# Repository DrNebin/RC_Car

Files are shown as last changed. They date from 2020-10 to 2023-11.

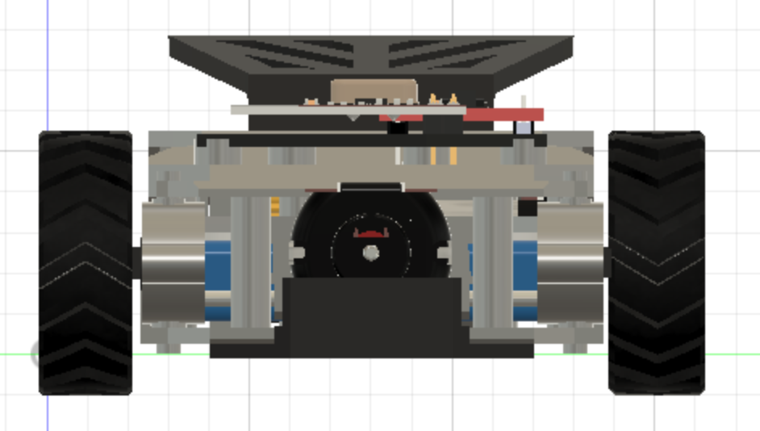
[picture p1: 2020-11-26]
RC_Car_RP/Photos and Video/CAD Design/Screen Shot 2020-11-26 at 4.18.56 AM.png

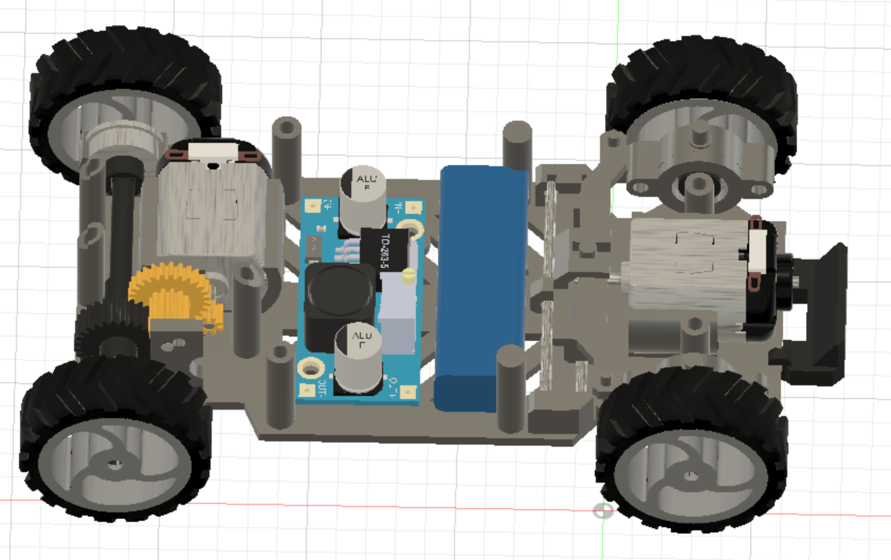
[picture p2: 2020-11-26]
RC_Car_RP/Photos and Video/CAD Design/Screen Shot 2020-11-26 at 4.21.05 AM.png

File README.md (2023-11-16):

# RC_Car (Devin Namaky)
My ongoing design for a SMALL RC Car 3D printable on a small resin printer driven by Arduino based electronics. Currently included here are two versions with all the schematics, PCB design (PCB prints are of course optional, but help decrease the footprint),  INO sketch files, STL files for printing, CAD files, etc. RC_Car_RP (Rack and Pinion) version uses two DC motors and a Seeeduino XIAO. The RC_Car_SS (Servo Steering) version uses one micro servo and one DC motor and an Arduino Nano. The RC_Car_SS Version is really a better design for several reason I won't belabor but if you want to build one of these cars, build RC_Car_SS.

# The main overarching objectives / themes of this project are
1. A small footprint - My benchmark is to be able to print it on an Original Elegoo Mars Resin 3D printer (Even the tires!).
2. Simple design - I have tried to minimize the number of parts.
3. Highly adaptable parts and electronics (Arduino-based) - My RC_Car_RP original prototype fit on one single 5x7cm protoboard and uses a Seeeduino XIAO. RC_Car_SS includes Servo steering, a new power setup with a momentary push button, and uses an Arduino Nano since more people have those on hand.
4. Easy to Build - To make wiring easier and further decrease size, I created PCB files and I've uploaded the Gerber files if you want to order your own PCBs, which I do recommend. 

# essential_Requirements for RC_Car
+ Car body width will not be less than 55 mm (so as to accept Seeeduino PCB, 5x7 protoboards, Double Feather setups, and Nano breakouts, etc.)
+ Car body length will not be less than 110 mm (gives room for steering motors, 130 style drive motor, and enough space to accept all the boards I just mentioned regarding width)
+ All components must be able to print on the original Elegoo Mars Resin Bed (68 mm x 120 mm). Note that the max Z height of the Mars is 150 mm. (Although, I acknowledge we are actually shooting to print with supports at about a 20 degree angle, which will decrease deformation.)
+ Must be rechargeable
+ Must be wireless (so I have also designed controllers)
+ It's a car

# RC_Car_RP (Rack and Pinion)
Don't build this version. I recommend you build the RC_Car_SS version.

Code for RC_Car uses the freely available libraries for nRF24 and SPI.

This project originated when I wanted to hack one of my kids small RC Cars that broke.

Just about any small microcontroller will do, but using here for RC_Car_RP a Seeeduino XIAO for the small footprint. 

The TB6612FNG Motor driver occupies PINs 0 thru 5 on the Seeeduino XIAO. You might notice an unexpected pinout order at pins 0 and 1. This is because I realized late in the game that pin 0 on the XIAO is not PWM.
The Wireless nRF24L01 SPI is on 8 thru 10, and CE / CSN are pins 6 and 7 on the XIAO.

This version is driving with two standard hobby 130 style DC motors, one for drivetrain and one for steering. The steering DC motor uses rack and pinion for steering in this first version. This allows the most commonly available and cheapest parts to be used.

Power setup is a 7.4V Lipo. The original was 850 mAh. It was a bit big and GAGA on the power and battery life so I am now using 300 to 400mAh capacity. This also allows the battery to fit on the lower plate with the step down unit. The battery runs on a toggle switch to a LM2596 to drop everything to 5V. The 5V is wired separately to the Seeeduino and the motor driver. Be aware, I did NOT use the VIN on the Seeed since it was not directly accessible by a pin on the PCB. I also wired the 5V to the standby pin of the motor driver so the motor driver is always in an "ON" state when the switch is turned on. Therefore, do NOT give this setup more than 5V from your step down power source or you will likely kill both the motor driver and the Seeeduino.

The rack and pinion steering system has been difficult to implement for several reasons, but after many prototypes I got it to work. It uses two metal rods of 2 mm in diameter (standard hobby rods) and two springs. I used a two inch spring from the local hardware store and cut it in half. I will be taking some measurements for lengths and updating them here. The rack gear slides along both of the rods, and the springs push against the rack gear from each side to re-center it. On my wish list was to develop a system that uses a torsion spring instead.

The rear gear system is 0.5 module. It uses the standard 8 tooth spur gear that comes with most 130 hobby motors. The middle gear converts from 12 teeth to 26 teeth, and the rear axle gear has 28 teeth. The middle great is supported by a short 2 mm standard hobby pin.

A bill of materials is posted.

# RC_Car_SS (Servo Steering)
This version is much improved and the one I recommend to build. It uses an Arduino Nano, an Adafruit momentary power switch, and an MG90s servo for the steering. Check out the Github folders for all the sketch files, schematics, fritzing file, Gerber files, chitubox files, STL files... everything really. I don't think Github will let me upload the Fusion 360 files but I'll give it a try. No Bill of Materials or instructions yet. Maybe I'll get to that one day.

# 3D Printing Notes
I used the original Elegoo Mars resin printer to print the car. Contrary to popular belief, you can absolutely print robust car parts, even on a resin printer. For many of the parts I used standard resin, especially if they were non-critical like the spoiler, or if I intended for them to be weaker anyway, like the bumper. For parts where strength is needed and for the gears there were two approaches I took that worked. One option is to use ABS-like resin, which I found acceptable. The other is to mix flexible or strength resins to the standard resin. I found 30% of Sirayatech Tenacious mixed with 70% of Standard Shine Tough Grey worked well and I favored that approach. For the standard resins, ABS-like and even the blend you can use pretty normal exposure and support settings if you limit the Tenacious to 30%.

Lastly, the TIRES! At first I tried standard resin and printed the wheel and tire together. As you can imagine there was no grip. Then I tried a "flexible" resin and used 100% Sirayatech Tenacious. Unfortunately, this was far from actually being flexible and still was very smooth and plastic like and did not provide any real traction either. Then I found Wanhao Rubber-like resin, and best of all it came in black. I would disagree that the resin is "rubber-like" in truth regarding flexibility. It's still actually pretty inflexible unless you are printing something thin. But it did provide enough flex to be able to print he tire separately and slip it over the wheel. The best part is that it did provide a rubber-like texture and feel and so it does provide grip and in the end worked well. 

The Wanhao took me four tries to successfully print as I had no real guidance. I found that I had to use 300% of normal exposure for the bottom layers, and 400% of normal exposure time for the remaining layers. My lift distance was 7 mm, bottom lift speed was 25 mm/min, lifting speed was 40 mm/min, and retract speed was 40 mm/min. The rubber-like resin really needs robust support. I had to double the diameter of my medium supports and the amount of contact depth, and I had to add large supports throughout the model. I think with good support I could probably back off on the exposure times a bit. The rubber-like prints take a very long time.

# RC_Car_CONTROLLER
Version 1 of the controller uses an Arduino NANO with two analog joysticks (right and left). Sends to the nRF24L01 on the car being controlled. You can use this controller for any RC project. It is highly adaptable. 

There are two joysticks. Joystick data can be processed a variety of ways. In this version the left joystick y-axis controls F / R, and the right joystick x-axis controls L / R. The right joystick push button is used to control the max motor speed. There are three different speed settings it toggles through. This is useful if you want to run the car indoor vs outdoor or simply don't want to strip your gears or crash into a wall with too much power depending on the power setup you choose.

Version 2 of the controller has many improvements and is the version I recommend you build. Version 2 is smaller, has a much larger broadcast range, uses a Lipo battery and even recharges it. It uses an Adafruit Itsy Bitsy 32u4 (3 volt version) with a Lipoly backpak. This particular board ends up being cool because it avoids the need for a step down unit and drives enough current to power the longer range nRF24L01+. It uses two joysticks again, but this time they are specifically the COM-09032 and directly soldered / connected to the PCB (no wires). You can get them from Sparkfun. Don't buy what looks like them on eBay. They will be the wrong size if you do.

Last note on Version 2 is that the Fritzing object has a bug that has a square copper connection for the positive lead on the capacitor, and a round one for the negative. The silkscreen includes a small negative sign that warns you of this. You can omit the capacitor if you have to.

Devin Namaky

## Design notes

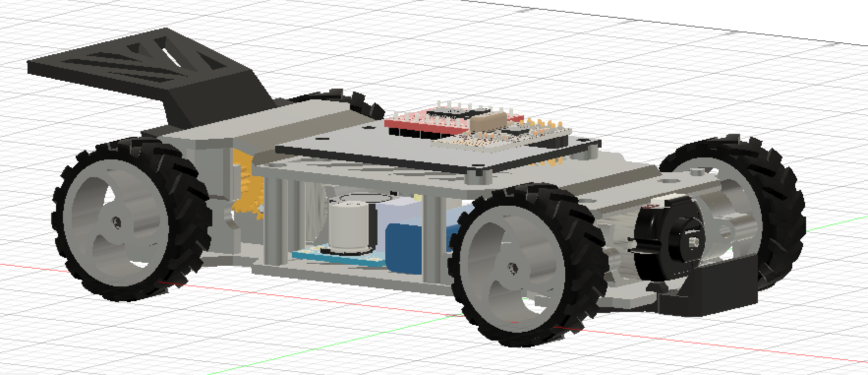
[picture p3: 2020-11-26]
RC_Car_RP/Photos and Video/CAD Design/Screen Shot 2020-11-26 at 4.18.32 AM.png

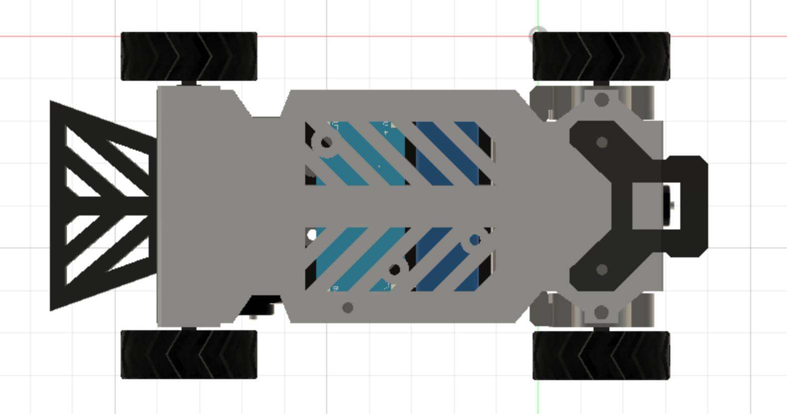
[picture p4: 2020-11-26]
RC_Car_RP/Photos and Video/CAD Design/Screen Shot 2020-11-26 at 4.19.42 AM.png

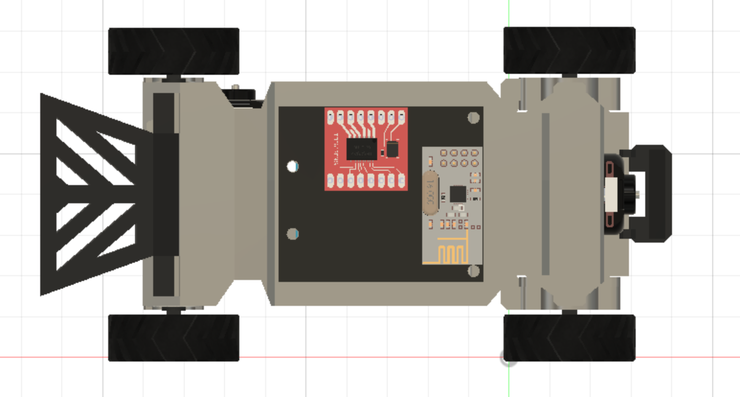
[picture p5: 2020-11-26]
RC_Car_RP/Photos and Video/CAD Design/Screen Shot 2020-11-26 at 4.19.57 AM.png

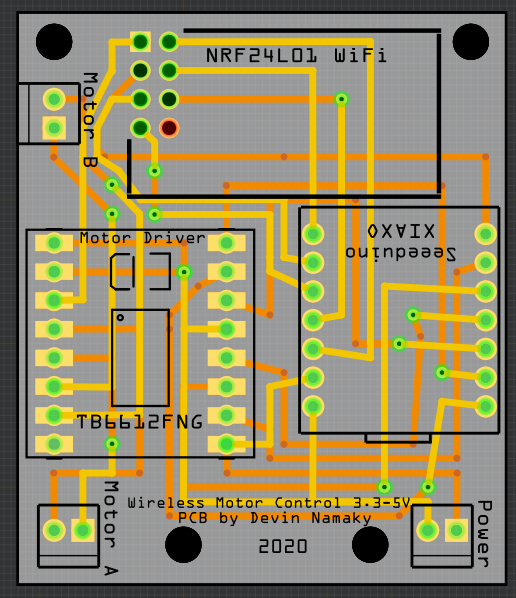
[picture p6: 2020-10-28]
RC_Car_RP/Schematics/Motor Board PCB.png

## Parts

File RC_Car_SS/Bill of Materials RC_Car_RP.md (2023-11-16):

#BILL OF MATERIALS 

This is the bill of materials for RC_Car_RP (Rack and Pinion). This is for the car only and does not include the wireless joystick controller.

I still haven't gotten around to adjusting this BOM for the SS version, but you can see most of them in the CAD file.  You can always message me for specific questions until I get around to it.

#Electronics

- Seeeduino XIAO, Qty. 1
- TB6612FNG Motor Driver, Qty. 1
- nRF24L01 Wireless module, Qty. 1
- Rocker switch, Qty. 1 (Any 2A capacity switch or higher should work)
- LM2596 DC Voltage Converter, Qty. 1 (Set for 5V output)
- 7.4V 2S Lipo Battery 300-400 mAh capacity (15 x 18 x 50 mm maximum dimensions)
- 130 Style DC Hobby Motor with included 0.5 module 8 tooth spur gear, Qty. 2
- Protoboard ~50 mm x 50 mm, or PCB ordered as designed (PCB recommended)

#Hardware

I bought the screws and springs at my local hardware store. I bought a 4 pack of the bearings online. The rods are easily found online or at your local hobby shop.
- Machine Screws, Size 4-40 x 1/4, Qty. 24
- FR188Z Bearings, Qty. 4
- 2 mm Hobby style metal rods, Qty. 3 (Cut to lengths of 48.5 mm (Qty. 2) and 16.5 mm (Qty. 1))
- 1 inch low tension spring approx. 1/4 in diameter, Qty 2. (I used a single 2 inch spring cut in half lengthwise)

#3D Printed parts (see Readme for printing suggestions)

STL files are provided for these parts:
- Spur gear 26-12, Qty. 1
- Rear Axle (includes axle gear), Qty. 1
- Rear Left Axle connector, Qty. 1
- Front Axle, Qty. 2
- Front Axle Retainer, Qty. 2
- Front Axle Bearing hub (Right), Qty. 1
- Front Axle Bearing hub (Left), Qty. 1
- Steering Rack, Qty. 1
- Steering Rod, Qty. 1
- Bottom plate, Qty. 1
- Top plate, Qty. 1
- Spoiler, Qty. 1
- Bumper, Qty. 1
- Tire, Qty. 4
- Wheel hub, Qty. 4

#Other useful supplies and tools

- Double sided tape to attach battery and rocker switch (Gorilla brand or similar)
- Misc Wires, heat shrink, nuts or other connectors
- Soldering iron, Solder and other soldering supplies
- Wire cutter and/or stripper
- Needle nose pliers
- Small screwdriver
- Tweezers
- File or rasp
- Small bolt cutter

#Programming

- Computer with Arduino IDE for programming the microcontroller, or a similar compatible setup
- Seeeduino boards installed on the IDE (If you have never done this, you will need to)
- Familiarize yourself with the process to reset the Seeeduino XIAO. It can be finnicky and may require a reset at some point while you are programming it.
- USB cable

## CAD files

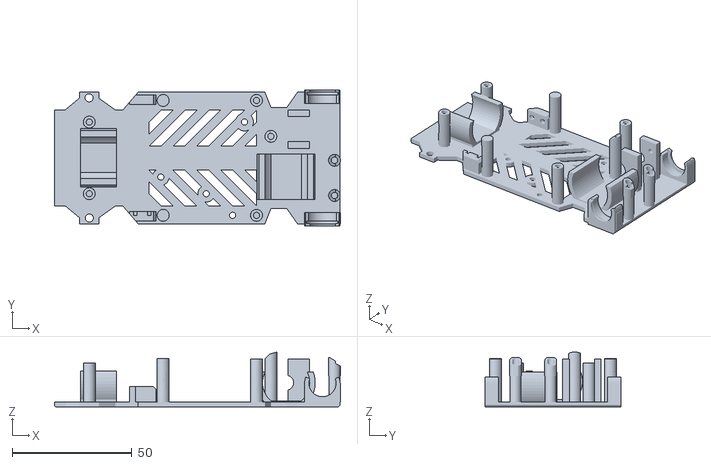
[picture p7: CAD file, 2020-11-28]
RC_Car_RP/STL/Body Bottom Plate.stl
119.5 x 57.0 x 22.9

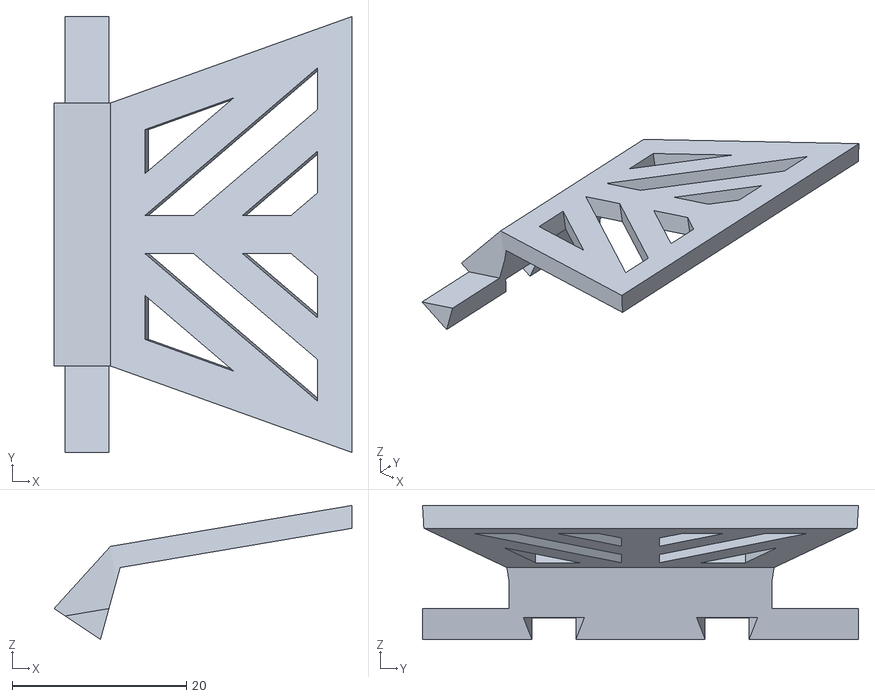
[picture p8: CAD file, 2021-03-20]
RC_Car_SS/STL/Spoiler.stl
34.2 x 50.0 x 15.4

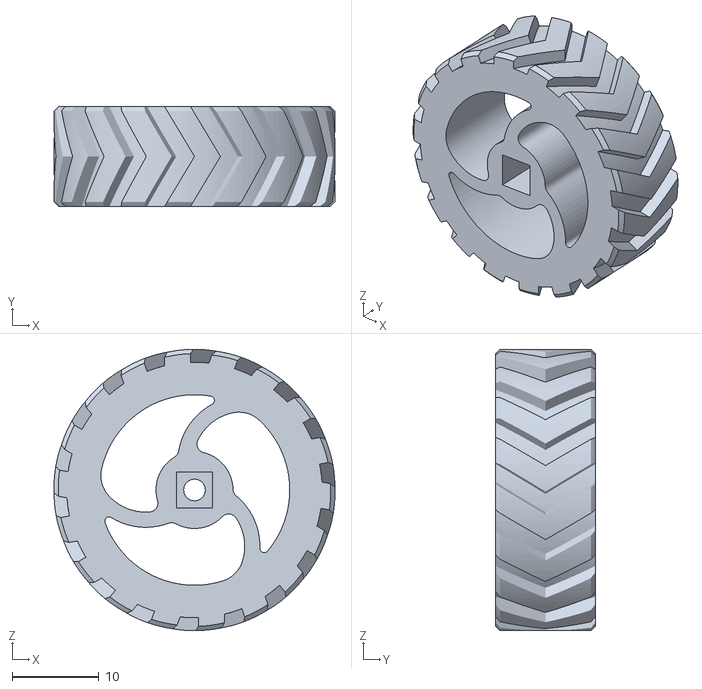
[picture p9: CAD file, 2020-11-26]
RC_Car_RP/STL/WHEEL AND TIRE.stl
32.5 x 11.5 x 32.5

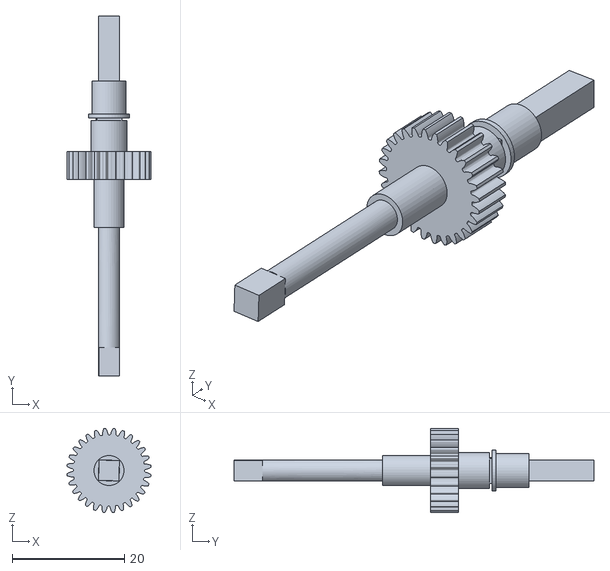
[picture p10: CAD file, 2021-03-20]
RC_Car_SS/STL/Rear Axle.stl
15.0 x 64.0 x 15.0

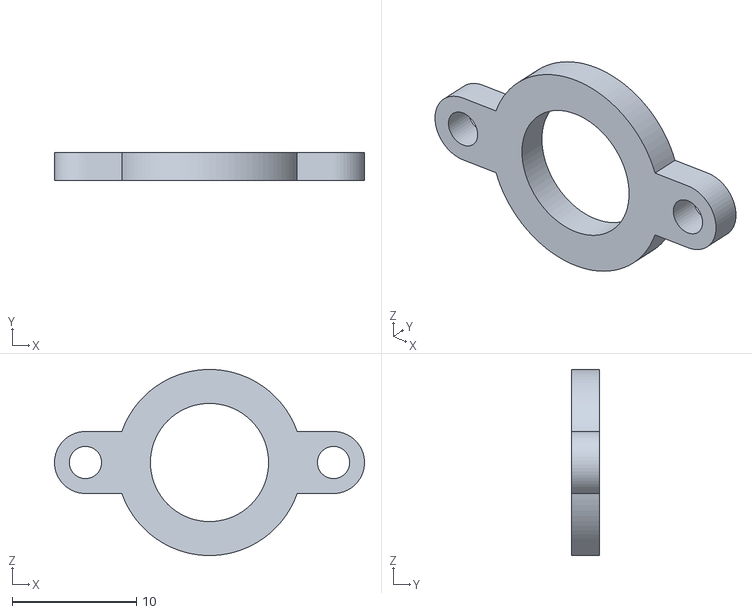
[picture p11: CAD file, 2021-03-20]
RC_Car_SS/STL/Inner bearing hub.stl
25.0 x 2.27 x 15.0

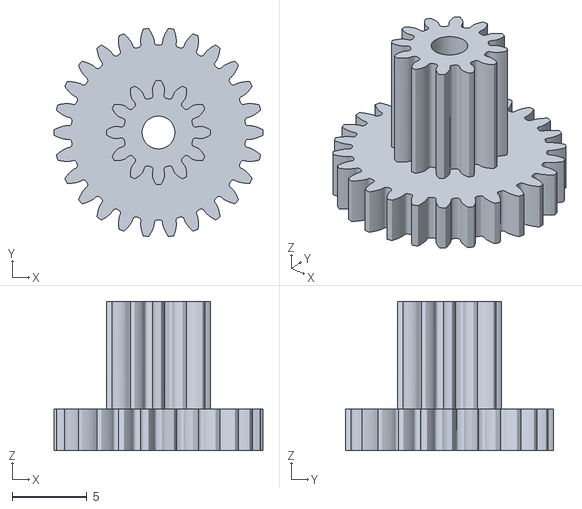
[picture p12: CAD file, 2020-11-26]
RC_Car_RP/STL/Spur Gear 26-12.stl
14.0 x 13.9 x 10.0

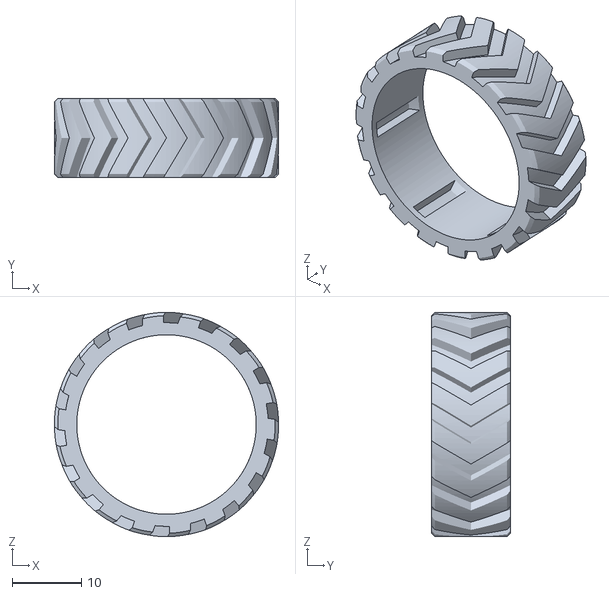
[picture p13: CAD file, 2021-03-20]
RC_Car_SS/STL/Tire.stl
32.5 x 11.5 x 32.5

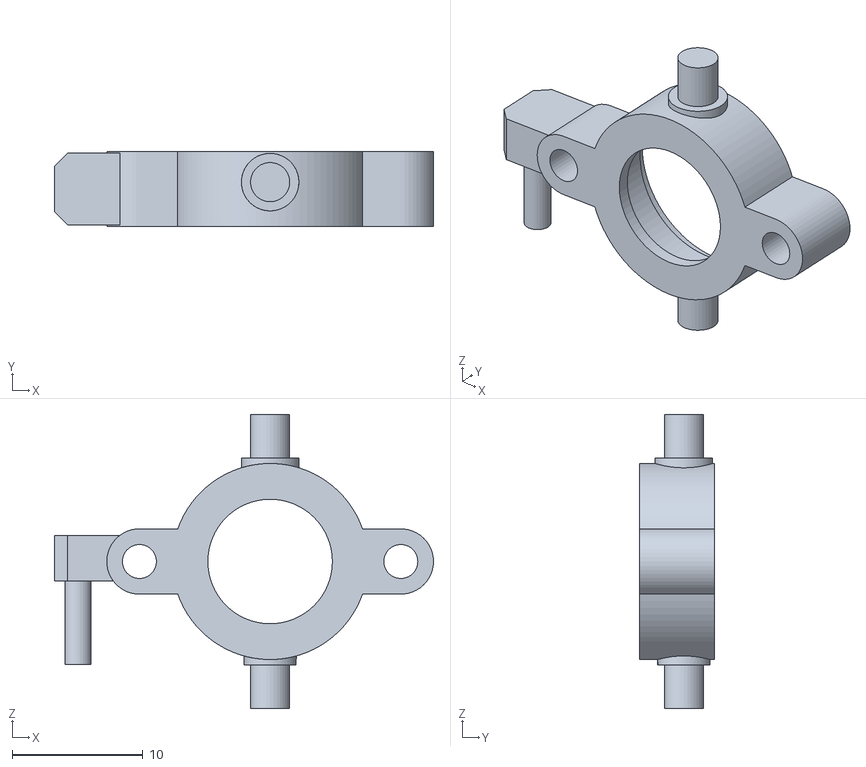
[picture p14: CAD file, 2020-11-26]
RC_Car_RP/STL/Front bearing hub outer right.stl
29.0 x 5.72 x 22.5

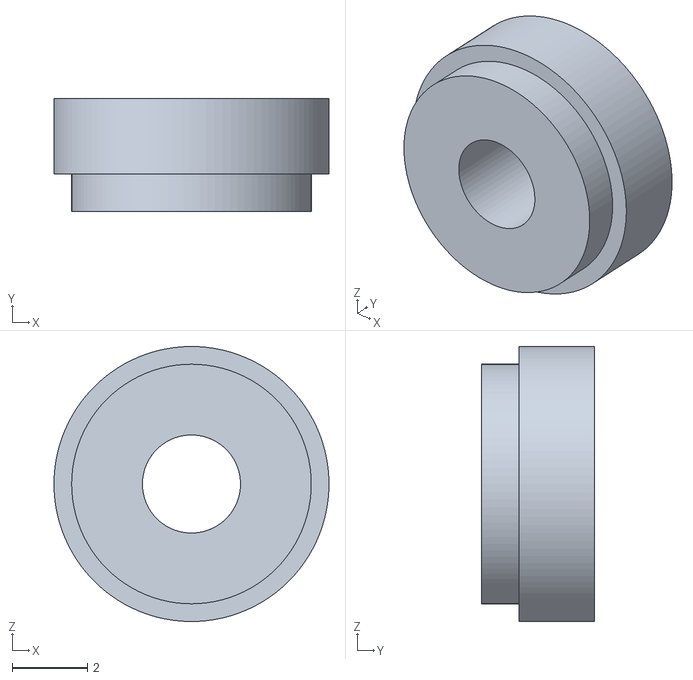
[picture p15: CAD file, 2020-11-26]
RC_Car_RP/STL/Front Axle Retainer.stl
7.29 x 3.00 x 7.29

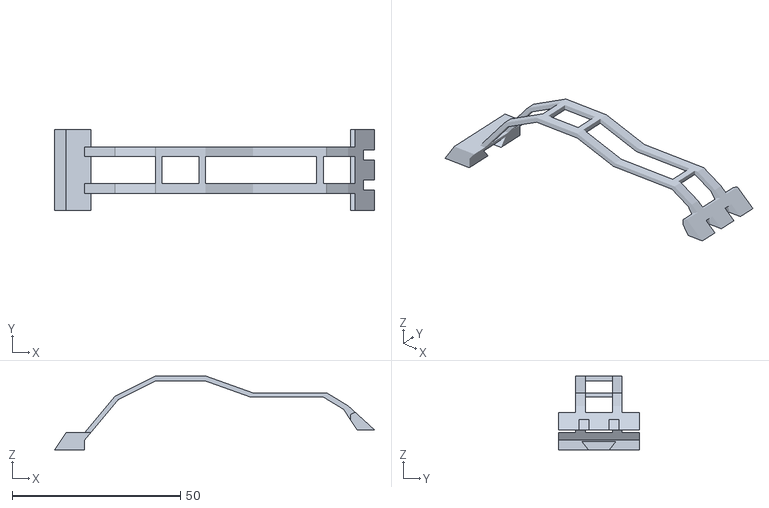
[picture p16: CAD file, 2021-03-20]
RC_Car_SS/STL/Roll Cage.stl
95.2 x 24.0 x 22.0

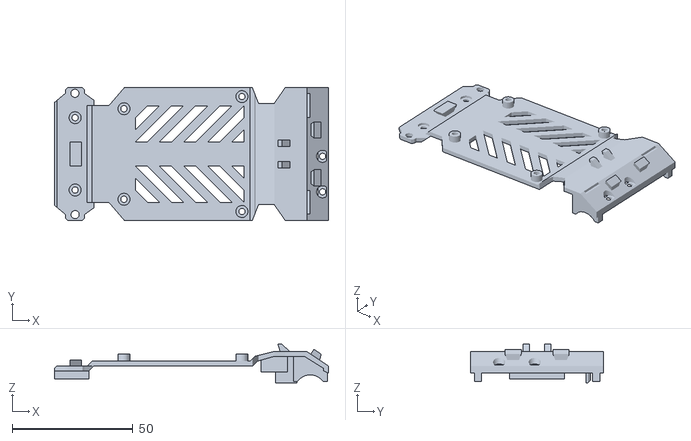
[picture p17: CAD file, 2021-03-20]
RC_Car_SS/STL/Top Plate.stl
113.5 x 55.0 x 15.9

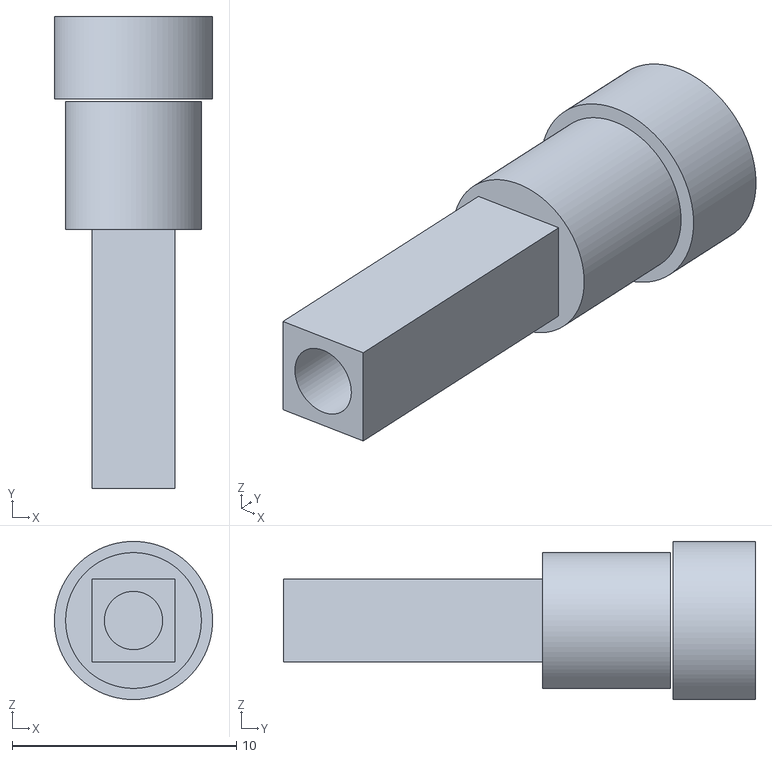
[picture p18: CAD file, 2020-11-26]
RC_Car_RP/STL/Left Axle Connector.stl
7.05 x 21.0 x 7.05

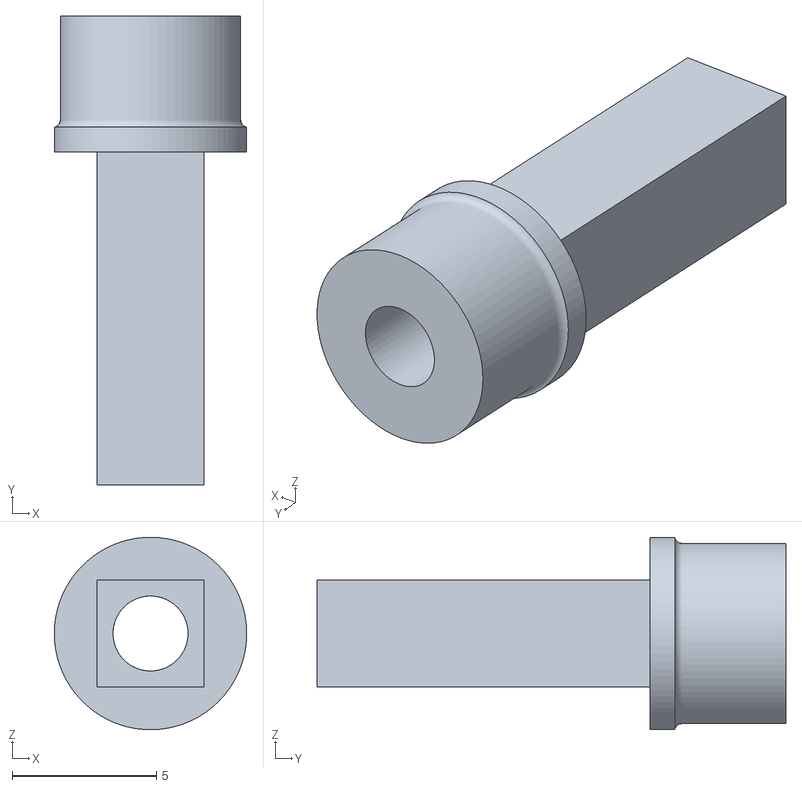
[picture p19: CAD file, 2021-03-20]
RC_Car_SS/STL/Axle.stl
6.67 x 16.2 x 6.67

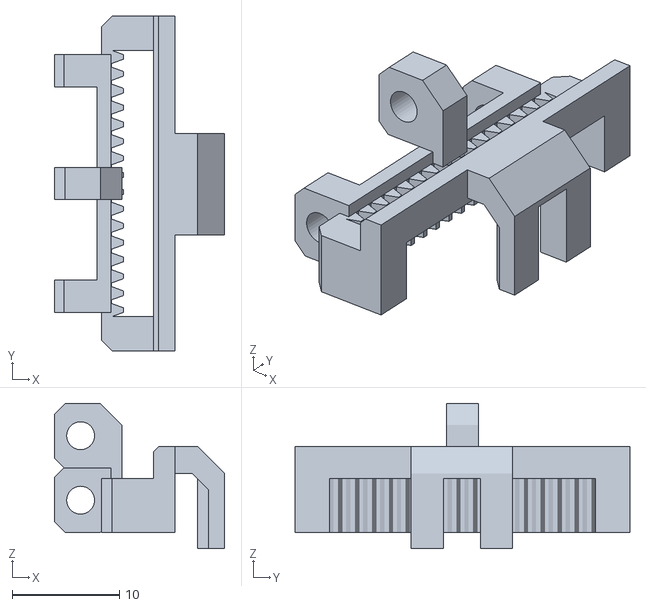
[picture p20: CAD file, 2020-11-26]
RC_Car_RP/STL/Steering Rack.stl
15.8 x 31.1 x 13.5

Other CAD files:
RC_Car_RP/STL/rear axle.stl
RC_Car_SS/STL/Spur Gear 26-12.stl
RC_Car_RP/STL/Front bearing hub outer left.stl
RC_Car_SS/STL/Left Front Bearing hub.stl
RC_Car_RP/STL/Axle.stl
RC_Car_RP/STL/Bumper.stl
RC_Car_RP/STL/Front bearing hub inner.stl
RC_Car_RP/STL/Spoiler.stl
RC_Car_RP/STL/Steering Rod.stl
RC_Car_RP/STL/Tire.stl
RC_Car_RP/STL/Wheel.stl
RC_Car_RP/STL/top plate.stl
RC_Car_SS/STL/Body Bottom Plate.stl
RC_Car_SS/STL/Bumper.stl
RC_Car_SS/STL/Front Axle Retainer.stl
RC_Car_SS/STL/Left Rear Axle Connector.stl
RC_Car_SS/STL/Right outer bearing hub.stl
RC_Car_SS/STL/Steering Rod Link.stl
RC_Car_SS/STL/Top Cover.stl
RC_Car_SS/STL/Wheel.stl

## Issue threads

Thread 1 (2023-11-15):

Specifications for the ball bearings

Shally1986, 2023-11-15:
Hello ,

I'm interested to build the rc car . Can you provide me the specification of the ball bearings needed

Thanks
Kushal

Shally1986, 2023-11-16:
Thanks for your reply.

Count is 4 ?

Thanks
Kushal Sahota

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

DrNebin, 2023-11-16:
Yes. DevinOn Nov 16, 2023, at 7:55 AM, Shally1986 ***@***.***> wrote:
Thanks for your reply.

Count is 4 ?

Thanks

Kushal Sahota

On Thu, 16 Nov, 2023, 6:03 pm DrNebin, ***@***.***> wrote:

> Closed #1 <https://github.com/DrNebin/RC_Car/issues/1> as completed.

>

> —

> Reply to this email directly, view it on GitHub

> <https://github.com/DrNebin/RC_Car/issues/1#event-10980052780>, or

> unsubscribe

> <https://github.com/notifications/unsubscribe-auth/BAOHSJZCNZV33634ZCSGYY3YEYBY3AVCNFSM6AAAAAA7MEUW2OVHI2DSMVQWIX3LMV45UABCJFZXG5LFIV3GK3TUJZXXI2LGNFRWC5DJN5XDWMJQHE4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>

> .

> You are receiving this because you authored the thread.Message ID:

> ***@***.***>

>

—Reply to this email directly, view it on GitHub, or unsubscribe.You are receiving this because you modified the open/close state.Message ID: ***@***.***>

Closed 2023-11-16.

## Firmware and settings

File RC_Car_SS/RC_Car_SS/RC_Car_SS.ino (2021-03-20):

// Arduino RC Car (RC_Car_SS) developed and programmed by Devin Namaky 2020 for his children
// This version uses an Arduino Nano on the car.
// Two generic joysticks for a remote. This version is wireless. There are separate INO and other files for two different versions of the controller on the Github. They both interface interchangeably with the car so pick whichever controller version suits you.
// Joysticks can be programmed a variety of ways. This version the left joystick y-axis controls F / R, and the right joystick x-axis controls L / R. The right joystick push button is used to control the max motor speed (cycles L, M, H). This is useful if you want to run the car indoor vs outdoor or simply don't want to strip your gears or crash into a wall with too much power depending on the battery setup you choose.
// Motor driver occupying PINs D6 thru D8 on the Nano as the below variables indicate.
// Wireless nRF24L01 SPI is on D11 thru D13, and CE / CSN are pins 10 and 9
// This version is driving with one DC motor for the drivetrain on a TB6612FNG, and one servo motor for steering on pin D5.
// All the schematics, code, fritzing, CAD and STL files are on my Github at https://github.com/DrNebin/RC_Car ; Also check out my blog for videos etc http://devinnamaky.com

//--------------DEFINITIONS & LIBRARIES--------------------//
#include <SPI.h>
#include <RF24.h>
#include <Servo.h>
RF24 radio(10, 9); // CE, CSN
const byte address[6] = "00001";

byte servoPin = 5;
byte PWMA = 6;
byte AIN1 = 8;
byte AIN2 = 7;
byte motorSpeedA = 0;
byte motorSpeedAMAX = 255; // Adjust for maximum power delivered forward to motor A (0 to 255)
const byte motorSpeedAReverse = 185; // Adjust for maximum power delivered reverse to motor A (0 to 255)
const byte servoNeutral = 65; // Adjust for neutral alignment of steering (0 to 180)
byte servoPosition; // stores the intended angle of the steering to be sent to servo
byte steerLeftAngleMAX = servoNeutral - 37; // enter value for max left turn angle of servo (0 to 90)
byte steerRightAngleMAX = servoNeutral + 37; // enter value for max right turn angle of servo (90 to 180)
unsigned long lastSpeedButtonReadTime = 0;
unsigned long lastControllerReadTime = 0;
unsigned long currentMillis = 0;

Servo steeringServo; // create the servo object

// -------construct NRF data package-----------//
struct Data_Package { // Create a single data package to be received over wireless
    byte joystick1xAxisBytes;
    byte joystick1yAxisBytes;
    byte joystick1Button;
    byte joystick2xAxisBytes;
    byte joystick2yAxisBytes;
    byte joystick2Button;
  };
Data_Package data; // Creates a variable "data" with the above structure of bytes
//--------------------------------------------//

//-----------------SETUP-------------------------------//
void setup() {
  servoPosition = servoNeutral; //startup with neutral alignment
  steeringServo.attach(servoPin);
  steeringServo.write(servoPosition);
  
  pinMode(PWMA, OUTPUT);
  pinMode(AIN1, OUTPUT);
  pinMode(AIN2, OUTPUT);
  
  Serial.begin(9600);  //NRF SETUP, OPEN PIPE, START LISTENING
  radio.begin();
  radio.openReadingPipe(0, address);
  radio.setAutoAck(false);
  radio.setDataRate(RF24_250KBPS);
  radio.setPALevel(RF24_PA_LOW);
  radio.startListening();
    // Reset data on startup to default values
  resetData();
}
//------------------------------------------------------//


//---------------------MAIN LOOP---------------------//
void loop() {
    //read controller data
    readController();
    //set motors
    setMotorSpeeds();
        // check the time
        currentMillis = millis();
        // check speed mode select button, including a 500 ms time period debounce
        // if receiving button data and the button is pressed, and the necessary time has passed
    if ((radio.available()) && (data.joystick2Button == LOW) && ((currentMillis - lastSpeedButtonReadTime) > 500)) {
        // then change the max speed
        if (motorSpeedAMAX == 120) {
            motorSpeedAMAX = 180;} else if (motorSpeedAMAX == 180) {
                motorSpeedAMAX = 255;} else if (motorSpeedAMAX == 255) {
                    motorSpeedAMAX = 120;
            }
        lastSpeedButtonReadTime = millis();
       //  Serial.println(motorSpeedAMAX);  // Serial printing generally commented out to save RAM unless debugging
    }
}
//------------------------------------------------------//

//---------------OTHER COMMAND DEFINITIONS----------------------------//
void resetData() { // Set the signals from the joysticks to neutral initially so the car doesn't move yet
    data.joystick1xAxisBytes = 127;
    data.joystick1yAxisBytes = 127;
    data.joystick2xAxisBytes = 127;
    data.joystick2yAxisBytes = 127;
    data.joystick2Button = 1;
    //     Serial.println("reset data"); 
  }

void readController() {
  if (radio.available()) {
    radio.read(&data, sizeof(Data_Package));
 /*    Serial.println("joystick1-Y: ");
     Serial.print(data.joystick1yAxisBytes);
     Serial.println("joystick2-Y: ");
     Serial.print(data.joystick2yAxisBytes);
      Serial.println("joystick1-X: ");
      Serial.print(data.joystick1xAxisBytes);
      Serial.println("joystick2-X: ");
      Serial.print(data.joystick2xAxisBytes);
      Serial.println("joystick2-Button: ");
      Serial.print(data.joystick2Button); */
      // Record the last time the controller was successfully read
      lastControllerReadTime = millis();
  }
    // Check the current time
  currentMillis = millis();
    // If the last successful control read is more than 1 second ago, reset the data to not lose control of the car
  if ((currentMillis - lastControllerReadTime) > 1000) {
    resetData();
    }
}

void setMotorSpeeds() {
        // Left joystick Y-axis used for forward and backward control
    if (data.joystick1yAxisBytes <= 123) {
      // Set Motor A direction
      digitalWrite(AIN1, LOW);
      digitalWrite(AIN2, HIGH);
      // Convert the declining Y-axis readings for going backward from 123 to 0 into 0 to max value for the PWM signal for increasing the motor speed
      motorSpeedA = map(data.joystick1yAxisBytes, 123, 0, 0, motorSpeedAMAX);
         Serial.println(motorSpeedA);
    } else if (data.joystick1yAxisBytes >= 132) {
      // Set Motor A direction
      digitalWrite(AIN1, HIGH);
      digitalWrite(AIN2, LOW);
      // Convert the increasing Y-axis readings for going forward from 138 to 255 into 0 to max value for the PWM signal for increasing the motor speed
      motorSpeedA = map(data.joystick1yAxisBytes, 132, 255, 0, motorSpeedAReverse);
    } else {
        motorSpeedA = 0;
    }
        if (motorSpeedA < 50) {   // prevent motor stall at low values
        motorSpeedA = 0;
    }
    // convert the right joystick value to an angle for the steering servo
    servoPosition = map(data.joystick2xAxisBytes, 0, 255, steerLeftAngleMAX, steerRightAngleMAX); 
    // eliminate neutral chatter when driving straight
    if ((servoPosition > 88) && (servoPosition < 92)) {
     servoPosition = servoNeutral;
    } 
    // finally write the determined speed and steering position to the motors
    analogWrite(PWMA, motorSpeedA);
    steeringServo.write(servoPosition);
}
//------------------------------------------------------//

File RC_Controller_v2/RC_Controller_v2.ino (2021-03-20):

// Uses an ItsyBitsy 23u4 with two analog joysticks (right and left). Sends to nRF24L01 on the car being controlled


//----------------DEFINITIONS AND LIBRARIES---------------------//
#include <SPI.h>
#include <nRF24L01.h>
#include <RF24.h>
RF24 radio(12, 13); // CE, CSN
const byte address[6] = "00001";

int joystick1ButtonPin = 10;
int joystick2ButtonPin = 11;

struct Data_Package {   // Create a single data package to be sent over wireless
  byte joystick1xAxisBytes;
  byte joystick1yAxisBytes;
  byte joystick1Button;
  byte joystick2xAxisBytes;
  byte joystick2yAxisBytes;
  byte joystick2Button;
  };
Data_Package data; // Creates a variable "data" with the above structure of bytes
//------------------------------------------------------//

//----------------------SETUP---------------------------//
void setup() {
  Serial.begin(9600);
  radio.begin();
  radio.openWritingPipe(address);
  radio.setAutoAck(false);
  radio.setDataRate(RF24_250KBPS);
  radio.setPALevel(RF24_PA_LOW);
  radio.stopListening();
  resetData();
  pinMode(joystick1ButtonPin, INPUT_PULLUP);
  pinMode(joystick2ButtonPin, INPUT_PULLUP);
}
//------------------------------------------------------//

//------------------MAIN LOOP------------------------//
void loop() {
  data.joystick1xAxisBytes = map(analogRead(A2), 0, 1023, 0, 255); // Read Joystick 1 X-axis and map to bytes
  data.joystick1yAxisBytes = map(analogRead(A1), 0, 1023, 0, 255); // Read Joystick 1 Y-axis and map to bytes
  data.joystick2xAxisBytes = map(analogRead(A4), 0, 1023, 0, 255); // Read Joystick 2 X-axis and map to bytes
  data.joystick2yAxisBytes = map(analogRead(A3), 0, 1023, 0, 255); // Read Joystick 2 Y-axis and map to bytes
  data.joystick1Button = digitalRead(joystick1ButtonPin);
  data.joystick2Button = digitalRead(joystick2ButtonPin);
  radio.write(&data, sizeof(Data_Package));   // Send the data package to the receiver

/*     Serial.print("joystick1-Y: "); // This section blocked out (for debugging if needed)
     Serial.print(data.joystick1yAxisBytes);
     Serial.print("joystick2-X: ");
     Serial.print(data.joystick2xAxisBytes);  */
}
//------------------------------------------------------//

//----------------OTHER COMMAND DEFINITIONS--------------//
void resetData() {  //resets joystick values to neutral
  data.joystick1xAxisBytes = 127;
  data.joystick1yAxisBytes = 127;
  data.joystick2xAxisBytes = 127;
  data.joystick2yAxisBytes = 127;
  data.joystick1Button = 1;
  data.joystick2Button = 1;
  }
  //------------------------------------------------------//

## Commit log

2020-10-28 Video of the original hack
    This is full power (255 PWM). I call it outside mode. I had to turn the power down to 90 of 255 PWM for it to be driveable indoors on our hardwood floors.
2020-10-29 Add power select and data reset
    Several improvements in this version. Added a data reset if the controller loses connection (so as not to lose control of the car), added MAX throttle toggle using the right joystick press to control low (indoor), medium (outdoor), and high (want to break the car?) throttle settings. Various cleanups and memory improvement also.
2020-11-26 Add files via upload
    CAD Design Photos Added
2020-11-27 Create Bill of Materials.md
2020-11-27 Create Bill of Materials RC_Car_V1.md
2020-11-27 Update Bill of Materials RC_Car_V1.md
2020-12-01 Model rename
    [Axle.stl, Body Bottom Plate.stl, Bumper.stl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]
2020-12-01 Model Renaming
    Various updates to improve model naming.
    [Axle.stl, Body Bottom Plate.stl, Bumper.stl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]
2021-03-20 RC_Car_SS Uploaded and many updates
    RC_Car_SS Uploaded and many updates
    [Axle.stl, Body Bottom Plate.stl, Bumper.stl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]
2023-11-16 Update Bill of Materials RC_Car_RP (not SS).md
